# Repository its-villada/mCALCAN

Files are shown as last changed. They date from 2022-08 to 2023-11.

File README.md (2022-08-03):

# mCALCAN
Satélite CANSAT del instituto técnico salesiano Villada. 
Este desarrollo responde a la iniciativa conjunta entre la Comisión Nacional de Actividades Espaciales (CONAE) y el Ministerio de Ciencia, Tecnología e Innovación (MinCyT) tiene como objetivo principal acercar la
ciencia y la tecnología a jóvenes en edad escolar, mediante la participación en la Convocatoria CANSAT Argentina.

## Objetivos
### Misión Primaria
Consiste en el sensado de presión y temperatura y la transmisión de esos datos a la estación terrena,al menos una vez por segundo. Mediante estos dos parámetros calcularemos la altitud, ya que tanto presión como temperatura varían con la altitud.
Para el cálculo de la altura, nuestro CANSAT transmitirá los datos de temperatura y presión antes del despegue y de esa manera obtener los datos iniciales necesarios para el cálculo.
### Misión Secundaria
Aprovechando y como complemento de la misión primaria, la misión secundaria consiste en medir la atmósfera y sus condiciones, con el objetivo de armar un perfil de atmósfera que pueda ser implementado, más adelante, como parte del modelo meteorológico internacional para la generación de pronósticos o la calibración de radares meteorológicos. Esto significa, que se medirán parámetros ambientales de presión y temperatura (tomados en la misión primaria), a los que agregaremos
humedad relativa y porcentaje de CO2. Estos parámetros son medidos y correlacionados con las coordenadas (latitud, longitud y altitud) obtenidas por un módulo GPS.

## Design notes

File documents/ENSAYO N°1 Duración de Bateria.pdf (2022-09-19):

## ENSAYO N°1: Proyecto Mcalcan

Autor: Equipo G.V.I.E

Objeto: Ensayo de duración de batería del CANSAT.

En este ensayo, planteamos experimentar y documentar la duración de las baterías encargadas de alimentar el CANSAT durante el tiempo de misión. Con esto podremos corroborar si la misión se podrá ejecutar con total normalidad con las baterías que contamos.

Condiciones de ensayo iniciales:

- Capacidad de la batería [mAh]: 600 mAh
- Consumo del CAN-SAT en modo operativo (picos): 800 mA
- Consumo del CAN-SAT en modo operativo (corriente promedio): 700 mA
- Voltaje de alimentación de entrada [V]: 7,4 V
- Tiempo de ensayo [m]: 60 m
- Muestras [m]: Cada 5 m

En esta oportunidad vamos a simular al consumo del CANSAT con una carga resistiva cuyo valor en ohmios nos pueda demandar la corriente deseada. Tomaremos muestras con un multímetro conectado a ambas baterías por separado para saber su voltaje.

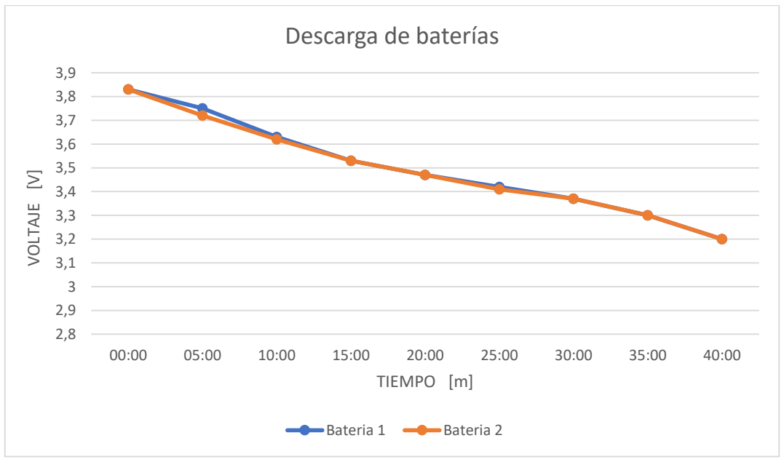
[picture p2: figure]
VOLTAJE [V]; TIEMPO [m]; Descarga de baterías; Bateria 1; Bateria 2

Conclusión: Finalmente llegamos a realizar el ensayo hasta pasados los 40 minutos, ya que las baterías habían llegado a su punto mínimo de descarga. Sin embargo, es una prueba contundente de que nuestra carga útil va a operar con normalidad en los 3-5 minutos que dura dicha misión.

Notas de aplicación:

Realizaremos un cálculo extrapolando la relación de descarga de las baterías en el ensayo previo.

Teóricamente con una batería en óptimas condiciones deberíamos tener, si consumimos 600mA, una duración de 1 hora. Luego del ensayo llegamos a la siguiente relación con respecto a las condiciones reales de la batería.

660mA = 40 minutos

Con esta relación podemos estimar distintos tiempos para distintos consumos. En el caso de que nuestra carga útil este en modo stand-by, consumiendo 100mA. Duraría lo siguiente.
(

660mA
100mA ) ∗ 40 minutos = 264 minutos

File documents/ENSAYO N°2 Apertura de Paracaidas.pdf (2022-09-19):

## ENSAYO N°2: Proyecto Mcalcan

Autor: Equipo G.V.I.E

Objeto: Ensayo de apertura de paracaídas.

En esta oportunidad, planteamos experimentar en la apertura del paracaídas del CANSAT. Para ello nos dirigiremos a las Jarillas, Córdoba (Coordenadas: -31.53743215294978, -64.54285469326625) donde se encuentra un puente con acceso al valle debajo de él. Allí soltaremos un CANSAT señuelo, que este compuesto de la misma estructura y peso que el original, pero sin el hardware dentro. Mediremos la velocidad de descenso y el tiempo de apertura y realizaremos 3 pruebas para poder llegar a un promedio.

Materiales para realizar el ensayo:

- Una balanza.
- Un cronometro.
- Papel y hoja.
- CANSAT señuelo.
- Paracaídas.

Condiciones del primer ensayo:

- Peso del CANSAT señuelo [g]: 306 g
- Medidas del paracaídas:

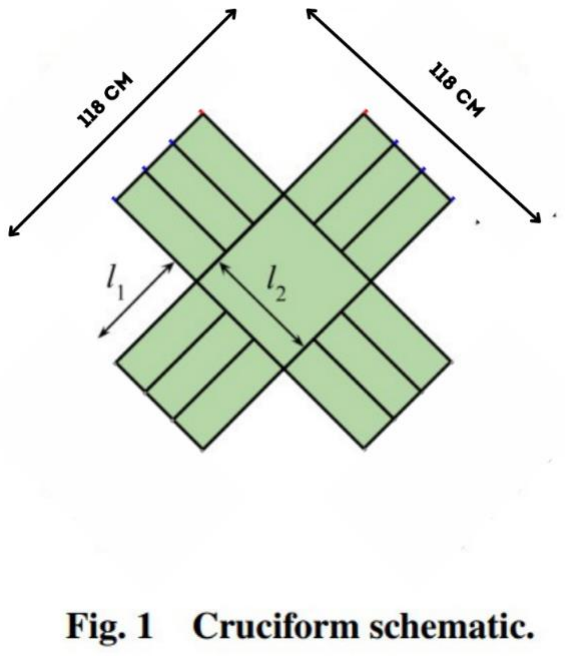
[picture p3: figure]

- Altura de caída libre [m]: 70 m
- Velocidad del viento [m/s]: 4 km/h

- Todos los hilos del mismo largo

Resultado:

El paracaídas al estar enrollado muy fuerte tardó cerca de 4 segundos en abrirse, por lo que tuvo menos desplazamiento en el plano horizontal y además la velocidad del viento era mínima. Sin embargo, en el instante que se abrió el paracaídas la velocidad de caída disminuyo demasiado, aproximadamente a 5,5m/s, lo cual es un punto a favor.

Condiciones del segundo ensayo:

- Peso del CANSAT señuelo [g]: 306 g.
- Medidas del paracaídas:

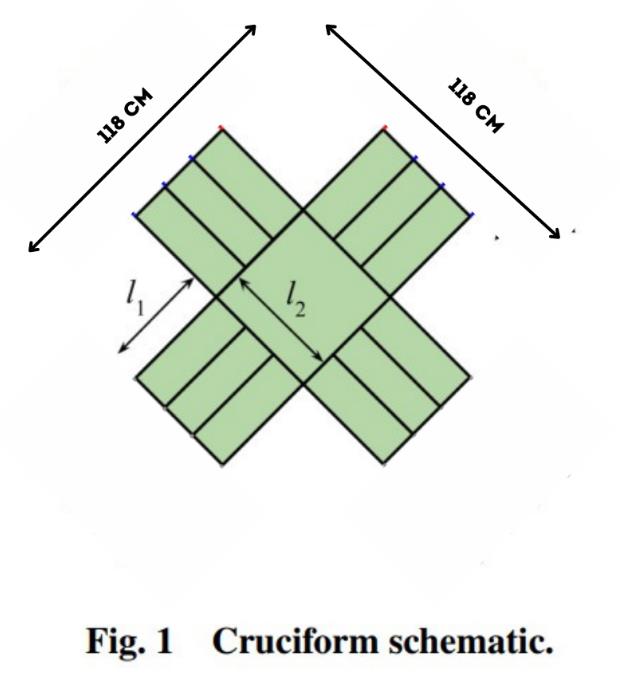
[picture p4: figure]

- Altura de caída libre [m]: 70 m.
- Velocidad del viento [m/s]: 15 km/h.
- Todos los hilos del mismo largo.

Resultado:

Esta vez al estar enrollado de una manera más leve, el paracaídas se abrió casi instantáneamente. A causa del fuerte viento el CANSAT tuvo un desplazamiento horizontal aproximado de 50m con una caída de una velocidad cerca de los 5 m/s.

Conclusión:

El paracaídas para que tenga una repuesta de apertura rápida se debe enrollar de una manera especifica con una tensión de hilos apropiada. Tiene una resistencia muy buena al aire y la tela sylver es la correcta para este tipo de paracaídas.

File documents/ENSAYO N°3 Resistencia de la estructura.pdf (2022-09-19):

## ENSAYO N°3: Proyecto Mcalcan

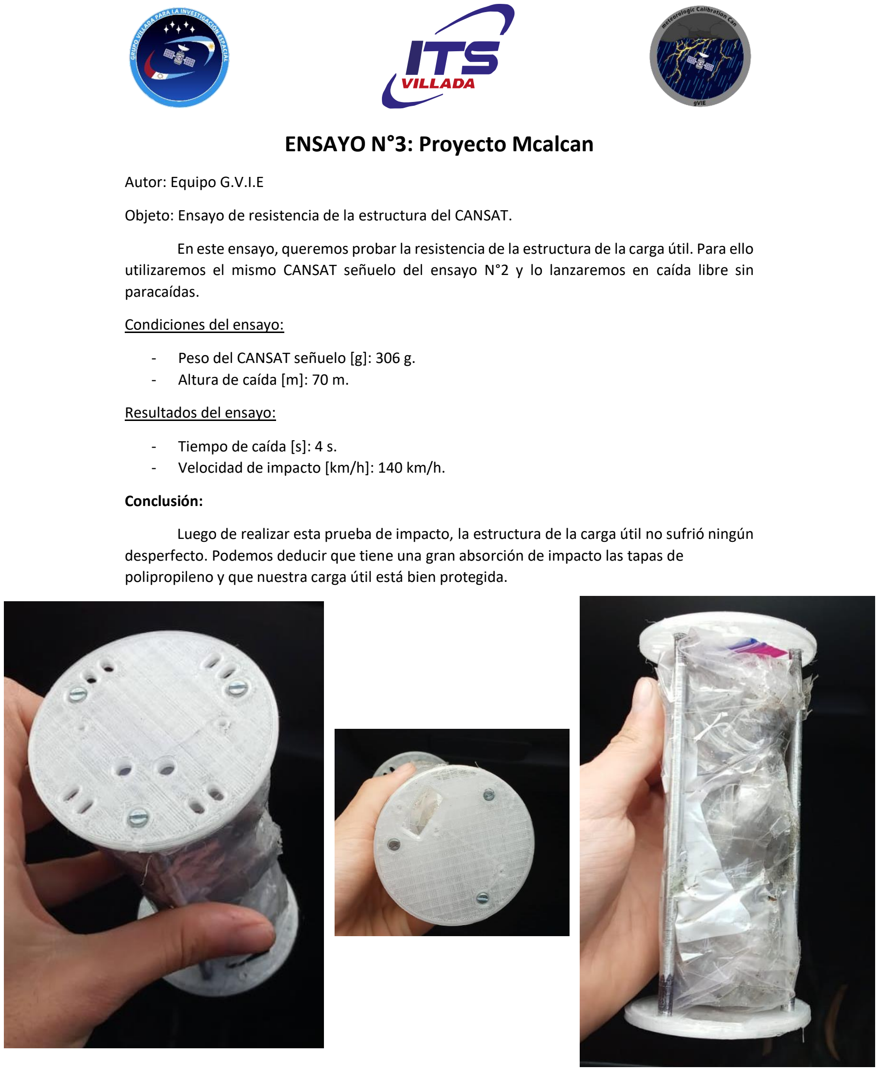
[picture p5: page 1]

Autor: Equipo G.V.I.E

Objeto: Ensayo de resistencia de la estructura del CANSAT.

En este ensayo, queremos probar la resistencia de la estructura de la carga útil. Para ello utilizaremos el mismo CANSAT señuelo del ensayo N°2 y lo lanzaremos en caída libre sin paracaídas.

Condiciones del ensayo:

- Peso del CANSAT señuelo [g]: 306 g.
- Altura de caída [m]: 70 m.

Resultados del ensayo:

- Tiempo de caída [s]: 4 s.
- Velocidad de impacto [km/h]: 140 km/h.

Conclusión:

Luego de realizar esta prueba de impacto, la estructura de la carga útil no sufrió ningún desperfecto. Podemos deducir que tiene una gran absorción de impacto las tapas de polipropileno y que nuestra carga útil está bien protegida.

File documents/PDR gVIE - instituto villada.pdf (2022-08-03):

# mCALCAN

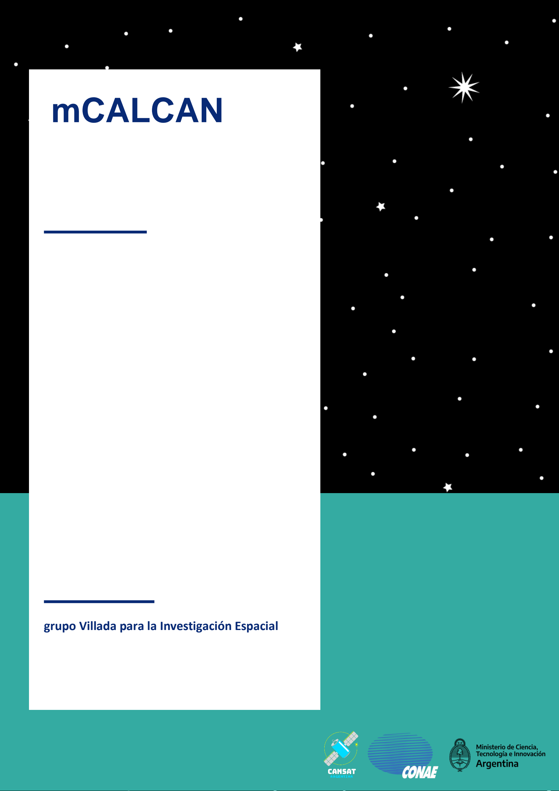
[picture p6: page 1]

1

grupo Villada para la Investigación Espacial

2

Introduccion _______________________________________________________________________ 3

Terminos a Utilizar __________________________________________________________________ 5

Mision ____________________________________________________________________________ 6

Objetivos_______________________________________________________________________________ 6 Misión Primaria ________________________________________________________________________________ 6 Misión Secundaria______________________________________________________________________________ 6

Diseño Preliminar________________________________________________________________________ 8 Layout Físico __________________________________________________________________________________ 8 Como Funciona: Operaciones _____________________________________________________________________ 8

Subsistemas ____________________________________________________________________________ 9 Microprocesador_______________________________________________________________________________ 9 Comunicaciones _______________________________________________________________________________ 9 Sensores _____________________________________________________________________________________ 9 Unidad de Potencia Eléctrica _____________________________________________________________________ 9 Control de Descenso ___________________________________________________________________________ 10 Estructuras __________________________________________________________________________________ 11 Presupuesto de Masas _________________________________________________________________________ 11

Software ______________________________________________________________________________ 12 Programación del Software de Vuelo ______________________________________________________________ 12

Estación Terrena________________________________________________________________________ 13 Configuración ________________________________________________________________________________ 13 Programación de la Estación Terrena ______________________________________________________________ 13

Integración y Pruebas ___________________________________________________________________ 14 Pruebas preliminares de los componentes__________________________________________________________ 14 Secuencia de Integración _______________________________________________________________________ 14 Pruebas de Integridad__________________________________________________________________________ 14 Plan de Validación_____________________________________________________________________________ 15

Operación de la Misión __________________________________________________________________ 16 Secuencia de Eventos prevista ___________________________________________________________________ 16 Roles y Responsabilidades ______________________________________________________________________ 17

Presupuesto ___________________________________________________________________________ 18

Capacidades ___________________________________________________________________________ 19 Capacidades de grupo__________________________________________________________________________ 19 Instalaciones y equipamiento ____________________________________________________________________ 20

Agenda _______________________________________________________________________________ 21

Plan de Documentación__________________________________________________________________ 22

Plan de publicación y Difusión de Resultados_________________________________________________ 23

Enlace al video de presentación ___________________________________________________________ 23

Anexos___________________________________________________________________________ 24

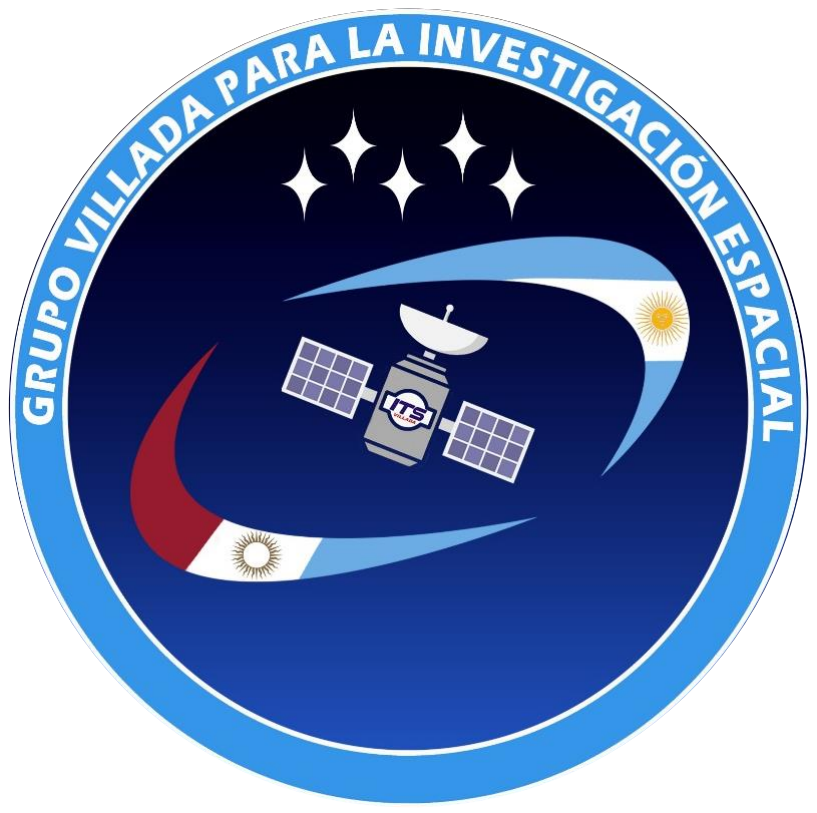
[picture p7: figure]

3

# Introduccion

Nombre del Equipo: grupo Villada para la Investigacion Espacial (gVIE)

Institución: Instituto Tecnico Salesiano Villada

Integrantes del Equipo:
CORTESINI, Luciano
GIL, Ignacio
GIRAUDO, Tomas
LOPEZ, Alejo
PALOMBO, Franco

Docentes:
BEDOURET, Martín
FERRARO, Federico

Parche:

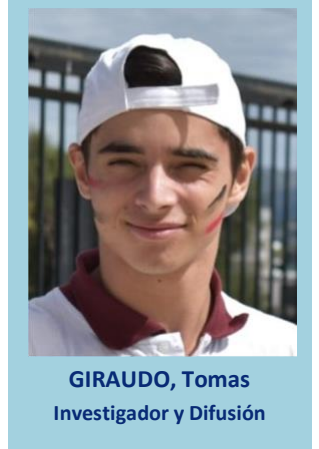
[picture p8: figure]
GIRAUDO, Tomas; Investigador y Difusión

4

Organización del Equipo: Roles

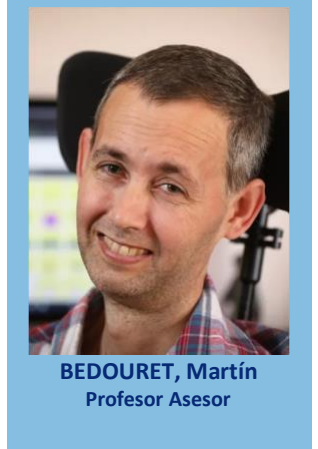
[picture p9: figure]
BEDOURET, Martín Profesor Asesor
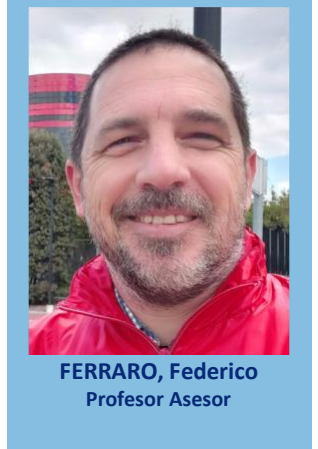
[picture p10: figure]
FERRARO, Federico Profesor Asesor
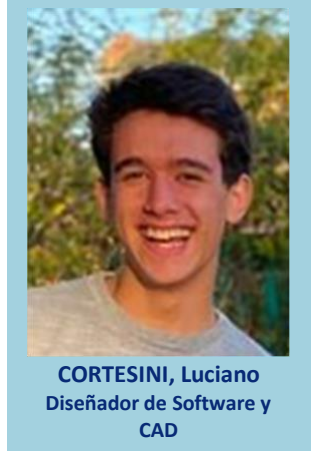
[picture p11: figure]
CORTESINI, Luciano Diseñador de Software y CAD
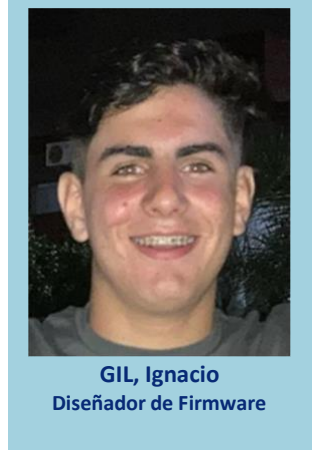
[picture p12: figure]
GIL, Ignacio Diseñador de Firmware
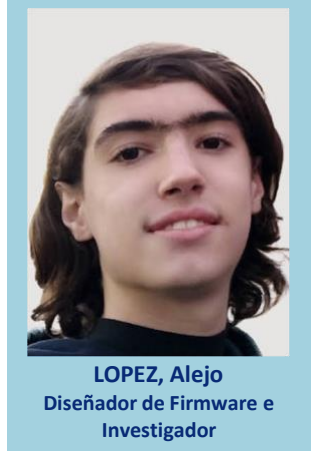
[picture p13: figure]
LOPEZ, Alejo Diseñador de Firmware e Investigador
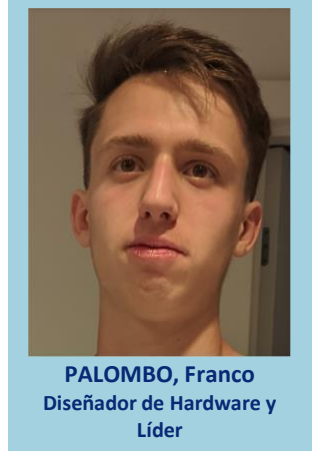
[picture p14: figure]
PALOMBO, Franco Diseñador de Hardware y Líder

5

# Terminos a Utilizar

CPU: Unidad de Procesamiento Central
MCU: Unidad de Microcontrolador
GPS: Sistema de Posicionamiento Global SwPS: Fuente de Alimentación Switching Li-Po: Polímero de litio

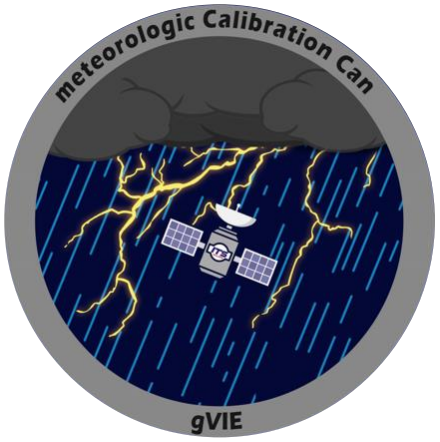
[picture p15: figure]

6

# Mision

Nombre de Mision: mCALCAN (meteorologic Calibration Can)

Parche:

## Objetivos

Misión Primaria
Consiste en el sensado de presión y temperatura y la transmisión de esos datos a la estación terrena, al menos una vez por segundo. Mediante estos dos parámetros calcularemos la altitud, ya que tanto presión como temperatura varían con la altitud.
Para el cálculo de la altura, nuestro CANSAT transmitirá los datos de temperatura y presión antes del despegue y de esa manera obtener los datos iniciales necesarios para el cálculo.

Misión Secundaria
Aprovechando y como complemento de la misión primaria, la misión secundaria consiste en medir la atmósfera y sus condiciones, con el objetivo de armar un perfil de atmósfera que pueda ser implementado, más adelante, como parte del modelo meteorológico internacional para la generación de pronósticos o la calibración de radares meteorológicos. Esto significa, que se medirán parámetros ambientales de presión y temperatura (tomados en la misión primaria), a los que agregaremos humedad relativa y porcentaje de CO2. Estos parámetros son medidos y correlacionados con las coordenadas (latitud, longitud y altitud) obtenidas por un módulo GPS.

El planteamiento de la misión secundaria ronda alrededor de los siguientes puntos:
- Alto costo de las radiosondas meteorológicas:

7

Las radiosondas meteorológicas son dispositivos diseñados para perderse, pero dados los requerimientos de precisión en las mediciones, y las condiciones a las que son sometidas, su costo es bastante elevado (U$D200 en el año 2020). El principio de funcionamiento es que un globo de aproximadamente 6m de diámetro, inflado con hidrógeno, eleva la radiosonda a 30km de la superficie a nivel del mar, para luego explotar y dejar caer la radiosonda de manera incontrolada.
- Inversiones térmicas o scattering de Bragg en las mediciones de las radiosondas
Una inversión térmica, es cuando la temperatura del aire, en vez de descender mientras subimos en altura, como es normal, va ascendiendo cada vez más. Esto genera distorsiones o mediciones erróneas a los radares meteorológicos, los cuales generan perfiles atmosféricos erróneos. La generación de perfiles de atmósfera ayuda a calibrar radares como los que tiene Argentina para poder identificar en ellos estos fenómenos.
- La disminución de los vuelos comerciales por la pandemia:
Esto ha contribuido a tener menos información meteorológica, ya que los aviones en sus ascensos y descensos recolectan estos datos y son utilizados para los modelos de pronóstico.

Este contexto, relevado en el Observatorio Hidrometeorológico de Córdoba, organismo que opera el Radar Meteorológico ubicado en Córdoba Capital, ha servido de input para la definición de nuestra misión secundaria.
Es por eso, que proponemos como solución, la misión mCALCAN. Una opción económica y reutilizable, que permite generar perfiles de atmósfera para poder mejorar las predicciones meteorológicas, y poder aportar al modelo meteorológico internacional más información.

8

## Diseño Preliminar

Layout Físico
Revisar el Anexo: Diseño Preliminar

Como Funciona: Operaciones
El comportamiento esperado del CANSAT es el siguiente:
1. Desde que el CANSAT es cargado en el Cohete, y hasta que inicie el lanzamiento, se mantendrá en reposo para ahorrar energía.
2. Apenas entre en vuelo, el CANSAT comenzará a registrar toda la información y será almacenada en una memoria local.
3. Al momento de la eyección, el CANSAT comenzara la transmisión de datos, mientras paralelamente, sigue almacenando más información. Esto lo hacemos ya que la frecuencia de muestreo guardada en la SD podrá ser mayor a la transmitida, además de para tener redundancia en el caso de una desconexión en la comunicación.
4. Una vez el CANSAT comienza a descender en caída libre, se abrirá el paracaídas, y el sistema de guiado por GPS entrará en juego para comenzar el sistema de fly-back. El CANSAT, tratara de “planear” hasta la ubicación indicada, por medio de actuadores que corrijan el curso de caída hacia el punto designado
5. Luego de que el CANSAT haya aterrizado, emitirá un pitido por medio de un parlante piezoeléctrico y transmitirá la ubicación latitudinal y longitudinal a la estación terrestre para que su localización y recuperación sea más fácil.

9

## Subsistemas

Microprocesador
Se utilizará el microcontrolador Bluepill STM32 provisto por CONAE y MinCyT para realizar la lectura, almacenamiento y transmisión de datos.

Comunicaciones
Se utilizará el módulo LoRA LORA32U4 II provisto por CONAE para la comunicación entre la estación terrena y el CANSAT. Existe la posibilidad que el módulo que está en el CANSAT sea modificado para remover el procesador que incluye el módulo, y solo tener instalado el empaquetado LoRA, sin el microcontrolador que viene incluido. En la estación terrena se utilizará un módulo LoRA idéntico al utilizado en el CANSAT, el cual también será provisto por CONAE. Este módulo LoRA se enlazará al CANSAT y transmitirá todo lo que reciba del mismo a una computadora, a través de un cable USB y el protocolo serial.

Sensores
- Sensor de Presión y Temperatura: BMP180/BMP280, Necesario para la misión
designada por CONAE.
- Sensor de Humedad relativa y Temperatura: AHT10, Se utilizará para medir la
humedad relativa de la atmósfera, necesario para la misión secundaria.
- Sensor de Aceleración e inclinación: MPU6050, este sensor reemplazará al
acelerómetro provisto por CONAE ya que posee giroscopio, lo cual nos permitirá conocer la velocidad angular del CANSAT.
- Sensor de calidad de aire: MQ135, mide múltiples gases tales como: NH3, NOx, Alcohol, Benceno, Humo y CO2. Este sensor nos permitirá conocer la contaminación atmosférica.
- Módulo GPS: uBlox NEO-6M, necesario para obtener las coordenadas del CANSAT y así georreferenciar los datos del perfil atmosférico. También se usará para el control de descenso.

Unidad de Potencia Eléctrica
Para la unidad de potencia eléctrica, se utilizará la batería Li-Po provista por CONAE, en conjunción con una fuente de alimentación switching doble, de tipo buck-boost, con salidas de 5v y 3,3v para poder alimentar todos los sensores y componentes. En caso de que la batería de 1200mAh provista por CONAE sea insuficiente, una batería alternativa sería una celda de Li-ion 18650 de 3.3v, la cual es más grande y pesada pero posee el doble de capacidad, unos 2400mAh.
A continuación, se presenta un cálculo con el tiempo estimado de duración de la batería, dados los cálculos aproximados de potencia, sin tener en cuenta la eficiencia de las fuentes switching:

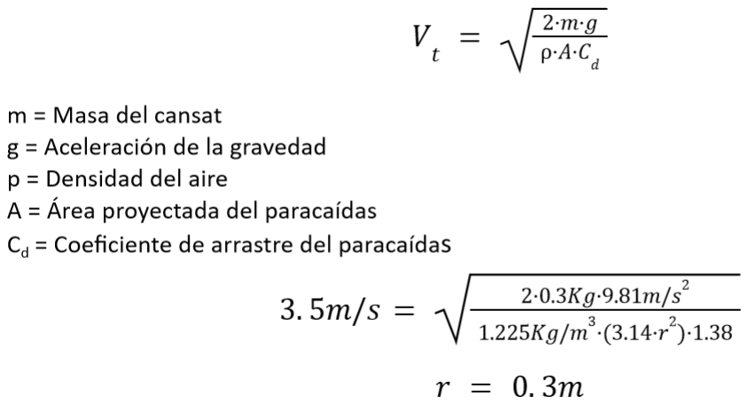
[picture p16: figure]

10

Componente Alimentación(nom) | Corriente(max) | Potencia(max)
STM32 (bluepill) | 3,3 v | 40 mA | 132 mW
LORA32U4 II | 3,3 v | 150 mA | 495 mW
BMP 180/280 | 5 v | 1 mA | 5 mW
MPU6050 | 3,3 v | 5,1 mA | 16,8 mW
uBlox NEO-6M | 3,3 v | 67 mA | 221,1 mW
AHT10 | 3,3 v | 23 uA | 70 uW
MQ135 | 5 v | 160 mA | 800 mW
MicroSD | 3,3 v | 150 mA | 495 mW
Subtotal | 3,3 v – 5 v | 537,12 mA | 2163,3 mW
Potencia Total Máxima Ptot(max) + 10% | 631 mA | 2379 mW

Con la batería que provee CONAE y MinCyT, podríamos tener una duración mínima de 1 hora y 53 minutos, por lo que en teoría, debería ser suficiente para completar la misión.

Control de Descenso
El control de descenso se basa en el objetivo de hacer que el CANSAT vuelva al punto donde despegó o intentar de acercarse lo más cerca posible. A este direccionado lo haremos a partir de un paracaídas que tendrá la posibilidad de ser piloteado a partir de un servomotor. En conjunto con el giroscopio y la ubicación GPS, sabremos hacia qué dirección debemos pilotear en CANSAT. Esto lo hacemos con la idea de poder recuperar el satélite y que no sea una misión de una única vez, sino que se pueda volver a lanzar el CANSAT.

Cálculo de las dimensiones del paracaídas
Para que el tiempo de descenso del CANSAT sea de 85 segundos este debe descender a una velocidad terminal de 3,5 m/s. Para lograr desacelerar la caída libre del cansat hasta la velocidad deseada el paracaídas utilizado será de forma cóncava y tendrá un radio de 0.3 metros. Estos valores se obtuvieron utilizando la fórmula de velocidad terminal, como se detalla a continuación.

11

Estructuras
La estructura de nuestro CANSAT estará formada por dos tapas de aluminio unidas a través de 3 varillas también de aluminio. Entre estas tapas, se colocarán de forma apilada los elementos necesarios, los cuales podemos dividir en 3 principales grupos.
- Sistema de control de descenso
Ubicado en la parte superior del CANSAT, donde se encontrará el servomotor encargado de controlar el paracaídas guiando así al satélite a punto de retorno
- Carga útil
Ubicada en la parte central del CANSAT, es donde se encuentran los sensores que utilizaremos para medir las variables físicas necesarias para cumplir la misión primaria y secundaria.
- Plataforma de servicio
En esta parte de la estructura se ubicarán todos los sistemas necesarios para que el CANSAT funcione: batería, sistema de potencia, sistema de control, comunicaciones.
Los elementos montados sobre las varillas principales de la estructura llevarán unos separadores que cumplirán la función de absorber las aceleraciones aplicadas al CANSAT, para de tal forma, cuidar la integridad de las partes.
Todo esto será recubierto por una carcasa de polipropileno impresa en 3D. Hacemos la elección de este material dadas sus características mecánicas como químicas, además de ser el material de más baja densidad que se comercializa para la impresión 3D por filamento. Para que los datos medidos sean confiables, esta carcasa deberá permitir el flujo de aire a la zona de la carga útil, evitando así fenómenos como el efecto Joule.
Además, la carcasa dispondrá de una apertura que permite remover la batería de CANSAT para su carga.
Presupuesto de Masas
Componente Cantidad | Peso Unitario | Subtotal
STM32 (bluepill) | 1 | 20 g | 20 g
LORA32U4 II | 1 | 20 g | 20 g
BMP 180/280 | 1 | 3 g | 3 g
MPU6050 | 1 | 2 g | 2 g
uBlox NEO-6M | 1 | 12 g | 12 g
AHT10 | 1 | 10 g | 10 g
MQ135 | 1 | 11 g | 11 g
MicroSD | 1 | 2 g | 2 g
PCB | 4 | 6,5 g | 24 g
Batería | 1 | 12 g | 12 g
Servomotor | 1 | 13 g | 13 g
Paracaídas | 1 | 25 g | 25 g
Tapa de Aluminio | 2 | 20 g | 40 g
Varillas de Aluminio | 3 | 10 g | 30 g
Tuercas de Aluminio | 6 | 1,5 g | 9 g
Carcasa Plástica (PP) | 1 | 20 g | 20 g
Separadores de PCB | 3 | 8 g | 24 g
Tornillería | | 20 g | 20 g
| | | TOTAL 297 g

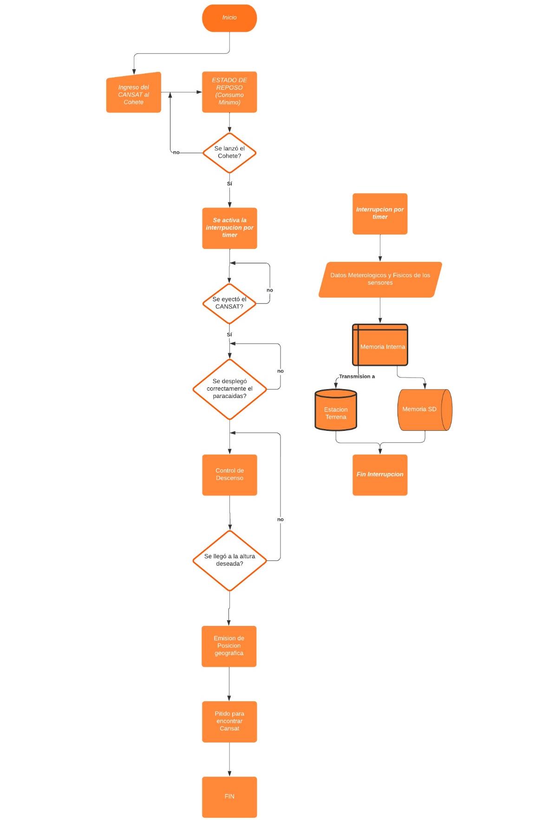
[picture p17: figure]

12

## Software

Programación del Software de Vuelo
Para la programación del software de vuelo, el lenguaje a utilizar, va a ser C y C++, el ide que se utilizará para programar ambos microcontroladores, tanto el bluepill stm32 como el ATmega32u4 de la placa de desarrollo LoRa, es el Arduino IDE, por su facilidad de uso y amplia disponibilidad de librerías y microcontroladores compatibles.

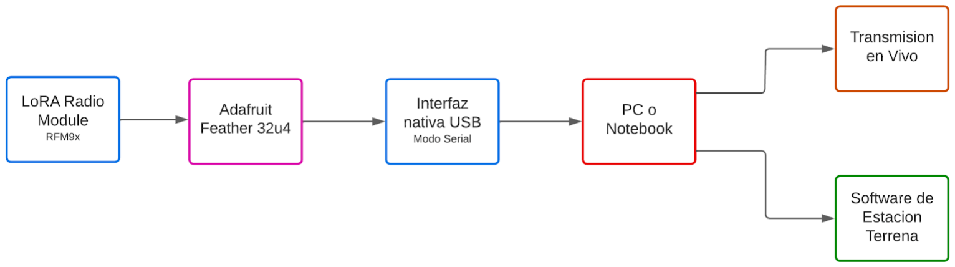
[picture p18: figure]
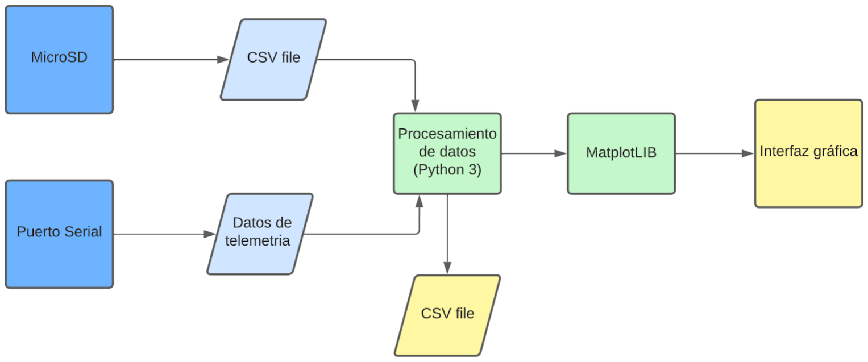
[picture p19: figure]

13

## Estación Terrena

Configuración
Diagrama en bloques del hardware:

Diagrama en bloques del software:

Programación de la Estación Terrena
La estación terrena estará equipada con un front-end con una interfaz de usuario que exponga múltiples gráficos sobre variables del CANSAT mismo, y los parámetros a medir, como también estados lógicos. Toda esta información será mostrada de dos formas:
a. Por medio de una computadora
b. Por medio de una transmisión por vía YouTube, con el agregado de una grabación en vivo del lanzamiento

El software de la estación terrena, desarrollado en Python 3, será capaz de leer desde el puerto serial de la computadora todos los datos recibidos por el módulo LoRa, mostrando a través de una interfaz gráfica todos los datos recopilados por el CANSAT y guardando estos datos en un archivo .CSV, además de mostrar valores de interés tales como nivel de batería, posición, etc.
Además, el software será capaz de leer el archivo .CSV guardado en la microSD del CANSAT y convertirlos en un gráfico para su fácil interpretación.

14

## Integración y Pruebas

Pruebas preliminares de los componentes
Todos los sensores serán testados individualmente previo al ensamblado del CANSAT y las mediciones serán contrastadas contra sensores calibrados, para asegurar el correcto funcionamiento de los sensores.
Para probar el funcionamiento de los módulos LoRA se establecerá un enlace simple entre dos computadoras cada una con su respectivo módulo y se comprobará el correcto envío y recepción de datos entre las mismas, así como el alcance y velocidad de enlace de los módulos LoRA.

Secuencia de Integración
1. Se parte de una base de aluminio la cual posee 3 varillas que cumplirán la función de columnas.
2. Se colocarán una por una las distintas PCBs las cuales poseen entre ellas un separador de goma.
3. Las PCBs se conectarán entre sí en el mismo momento de colocación ya que poseerán pines macho-hembra que entrarán en contacto al colocar la placa.
4. En la parte superior se colocará el sistema de control de descenso.
5. Se colocará la tapa superior del cilindro la cual se asegurará a las columnas a través de una tuerca y contratuerca,
6. Se colocará el cilindro exterior de la estructura(carcasa), el cual irá fijado a través de tornillos.
7. Se coloca, fija y conecta la batería a través de la apertura de la carcasa destinado a esto
8. Se fijará el paracaídas a la tapa superior con la ayuda de las ranuras destinadas a esto.
9. Se realizarán las pruebas de integridad y comunicaciones.
10. El CANSAT se encuentra listo para colocarse en el cohete.

Pruebas de Integridad
Una vez ensamblado el CANSAT se realizarán ensayos no destructivos para asegurarnos de que todos los subsistemas cumplan su función adecuadamente.
Se lanzará el CANSAT desde distintas alturas y con variadas velocidades angulares para comprobar el descenso controlado. Durante estas pruebas nos aseguraremos de no dañar la estructura del CANSAT. Para asegurarnos que el CANSAT siga funcionando, es decir siga midiendo correctamente los parámetros ambientales y enviando los datos a la estación terrena, pese a las altas aceleraciones y vibraciones, buscaremos alguna manera de probar el CANSAT en condiciones lo más similares posibles a las condiciones que existirán durante la misión.
Se encenderá el CANSAT y se dejará en estado de reposo (estado previo al lanzamiento) y en estado activo (Recopilando datos y enviándolos) durante tiempos varias veces mayor al que existirá durante la misión, esto para asegurarnos que no existan fallas en el código, como overflows de memoria o loops infinitos imprevistos, también para comprobar el comportamiento de la batería.

15

Plan de Validación
Para validar que nuestro CANSAT cumpla con los requerimientos de tamaño y peso determinados por el CONAE, imprimimos en 3D un cilindro cuyas dimensiones internas sean las máximas permitidas y nos aseguraremos de que nuestro CANSAT entre dentro de este cilindro. Para validar el peso del CANSAT utilizaremos una balanza de precisión.
Se prevee la fabricación de un “CANSAT dummy” con los mismos materiales, pesos y tamaños que el CANSAT final. Este dummy será lanzado desde una altura determinada, usando el sistema de descenso controlado diseñado por nosotros, los datos recopilados durante esta prueba luego se extrapolan para obtener una aproximación al comportamiento del CANSAT durante la misión. Este dummy también se utilizará para realizar ensayos destructivos y comprobar la integridad y resistencia física de nuestro CANSAT.

16

## Operación de la Misión

Secuencia de Eventos prevista
La misión se va a separar de 7 etapas:
- Etapa 1: Preparación de la estación terrena
Esta etapa es la que se ejecuta al llegar al lugar de lanzamiento. Consta de preparar la transmisión en vivo por la plataforma YouTube, la puesta en marcha de los programas de monitoreo y recepción y la conexión con el CANSAT y la Estación Terrena.
- Etapa 2: Prueba de comunicación y Prueba de sensores
Esta etapa es más que nada una verificación redundante, pero nos asegura la puesta en punto de los sensores y su correcto funcionamiento. En esta instancia, nos conectaremos al CANSAT desde la Estación terrena, y trataremos de simular algunas de las situaciones que se puedan presentar durante el lanzamiento (cambios de temperatura, %HR, y otros) para poder confirmar el correcto funcionamiento de todos los sensores.
- Etapa 3: Preparación para el lanzamiento
En esta etapa, se realizará la instalación del CANSAT en el cohete, y se colocará en modo de suspensión para ahorrar batería hasta que la interrupción indicada lo despierte.
- Etapa 4: Lanzamiento y Alcance del Apogeo
Durante esta etapa, se realizará un monitoreo básico y de baja frecuencia de las condiciones internas del CANSAT, tales como tensiones, temperaturas, posición y aceleraciones.
- Etapa 5: Recolección de datos en tiempo real y recuperación del CANSAT
Esta etapa consta de la recepción de la información en tiempo real que recupera el CANSAT, desde que llega al apogeo, hasta entrar en contacto con la superficie. Una vez llegado a la superficie, un equipo va a buscar el CANSAT en las coordenadas que transmitió antes de caer para recuperar la tarjeta de memoria.
- Etapa 6: Procesado de la información en tiempo real y local del CANSAT
Esta etapa consiste en comparar la información recibida y la información que se almacenó de manera local en el CANSAT para poder hacer gráficos, y poder confirmar que la información que se envió es la misma que está almacenada de manera local.
- Etapa 7: Compilación de información recogida
En esta etapa, se conformarán gráficos y resultados de fórmulas que serán los cuales serán utilizados más adelante para calibrar radares y modelos meteorológicos.

17

Roles y Responsabilidades
Franco Palombo: Supervisor de la misión
Tomas Giraudo: Encargado de difusión y transmisión en vivo
Luciano Cortesini: Operario de la Estación Terrena
Alejo López: Preparación y lanzamiento del CANSAT / recuperación del CANSAT Ignacio Gil: Preparación y lanzamiento del CANSAT / recuperación del CANSAT

18

## Presupuesto

Denominación Nro. de Mod. | Precio Unit. | Cantidad Subtotal
Sensor de Humedad y
Temperatura
| AHT10 | 600 AR$ | 1 | 600 AR$
Acelerómetro + Giroscopio | MPU 6050 | 700 AR$ | 1 | 700 AR$
Sensor de calidad de Aire | MQ135 | 550 AR$ | 1 | 550 AR$
Modulo GPS | uBlox NEO-6M | 2000 AR$ | 1 | 2000 AR$
PCB Virgen | 10x10cm | 300 AR$ | 2 | 600 AR$
Impresiones 3D | - | 300 AR$ | 1 | 300 AR$
Componentes Discretos/pasivos | - | 500 AR$ | 1 | 500 AR$
Varillas de Aluminio | D5mm L13mm | 250 AR$ | 3 | 750 AR$
Tornillería | - | 500 AR$ | 1 | 500 AR$
Círculos de Aluminio | D7mm E2mm | 50 AR$ | 2 | 100 AR$
TOTAL 6600 AR$

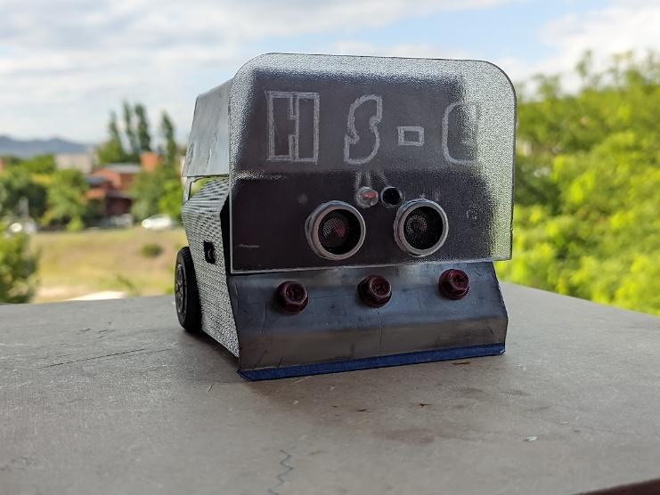
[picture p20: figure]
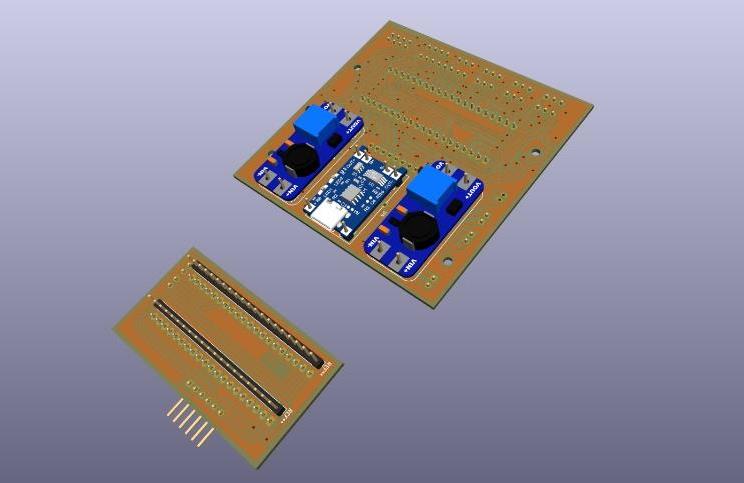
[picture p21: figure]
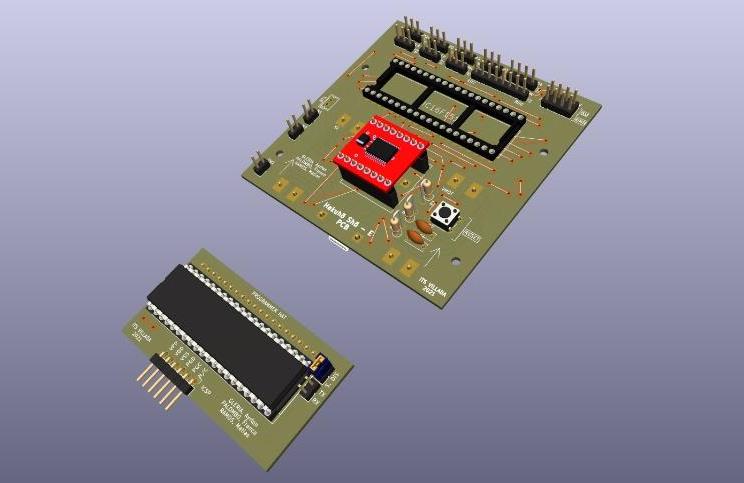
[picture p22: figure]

19

## Capacidades

Capacidades de grupo
Somos alumnos de 7mo año de un colegio técnico, con especialidad en electrónica. Por lo que nuestro grupo posee plena capacidad para llevar a cabo la misión CANSAT. Tenemos experiencia en el diseño y armado de circuitos impresos (PCBs), programación de microcontroladores con el lenguaje C, electrónica discreta, diseño e impresión 3D.

Nuestra participación en las Olimpiadas Nacionales de Innovación, Informática, Electrónica y Tecnología aplicada (ONIET 2020)
- Luciano Cortesini: 2do puesto en electrónica discreta
- Franco Palombo: 2do puesto en programación de microcontroladores.
- Ignacio Gil: 3er puesto en programación de microcontroladores.

Algunos ejemplos de nuestras capacidades en proyectos anteriores
Este proyecto es un Mini-sumo llamado “Hakuhō Shō – E”. Fue llevado a cabo durante el ciclo lectivo 2021. El objetivo de este proyecto era competir con otros grupos (de 3 integrantes) de alumnos del mismo colegio para determinar quién destacaba más en 3 áreas: Diseño de firmware automatizado, Diseño de Hardware y estrategia de trabajo.

20

Instalaciones y equipamiento
Contamos con un laboratorio de electrónica completamente equipado. Tenemos lo necesario para el armado de PCBs desde cero (Ácido, planchas, placas vírgenes, soldadoras, perforadora dremel), contamos con instrumentos de medición eléctrica como multímetros y osciloscopios, herramientas para la construcción de la estructura del CANSAT, impresoras 3D y demás herramientas para llevar a cabo la misión. También contamos con talleres mecánicos, con tornos, fresadoras, plegadoras de chapa, perforadoras, herramientas de corte y los materiales necesarios para fabricar la estructura del CANSAT.

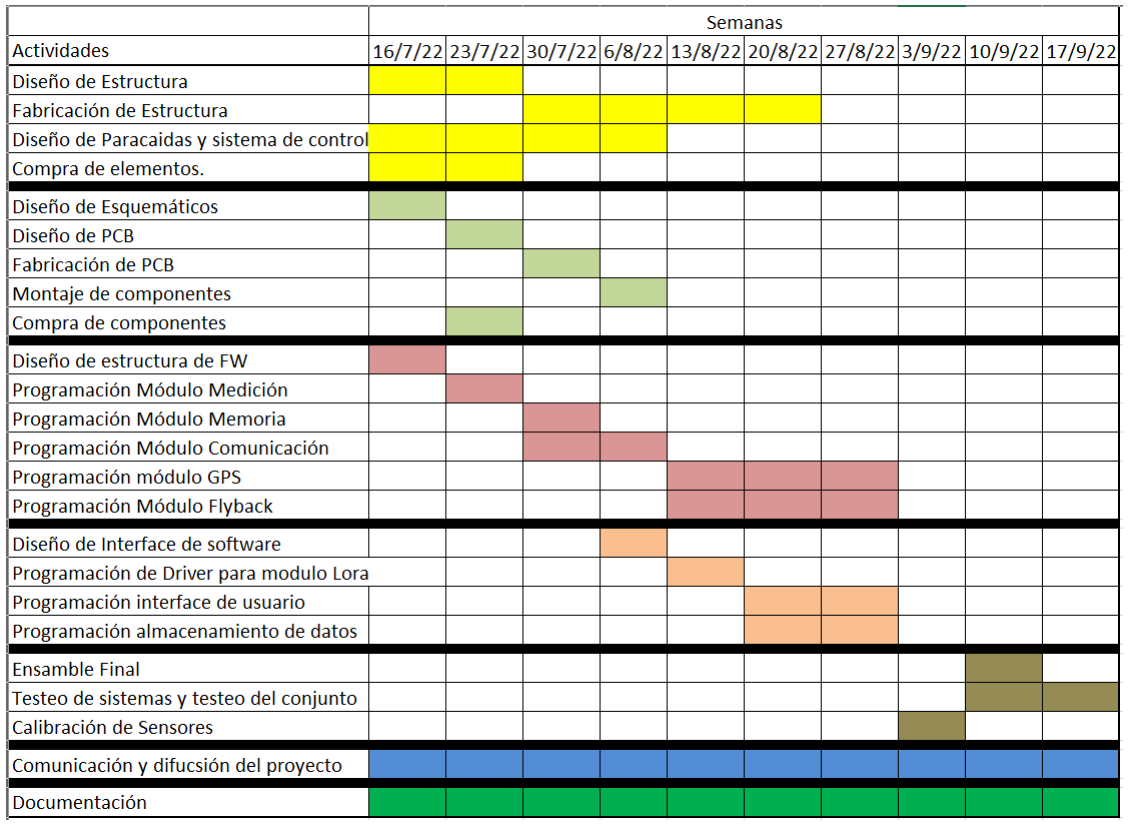
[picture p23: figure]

21

## Agenda

22

## Plan de Documentación

El plan de documentación que hemos planeado para este proyecto consiste en archivar todos los aspectos del mismo, por medio de la plataforma de GitHub y un drive de Google con acceso gratuito como lector. En ellos incluimos fotos, videos, códigos de programación, progreso del proyecto, diseños, etc.
Todos los enlaces con acceso a estas distintas plataformas, serán compartidos por nuestras redes sociales planteadas en nuestro plan de difusión.

23

## Plan de publicación y Difusión de Resultados

Nuestro plan de Difusión y Publicación de nuestro proyecto CANSAT de tanto, nuestro trayecto inicial como los procesos de fabricación y lanzamiento, se dirige a dos tipos de públicos.
- El primer objetivo de publicidad va destinado a investigadores, científicos, meteorólogos, integrantes de la CONAE, que quieran conocer los datos que pudimos recolectar en nuestra misión mCALCAN. La manera de poder difundir estos datos para que sean accesibles dentro de la comunidad científica es por medios de documentos científicos publicados en plataformas de lectura libre, como lo es la biblioteca virtual del CONICET. De esta forma, podemos generar un gran impacto dentro de la comunidad científica y podremos dar a conocer nuestro proyecto CANSAT
- El segundo objetivo, es poder llevar CANSAT a todas las escuelas del país para que la conozcan, por medio de redes sociales (como Instagram, You-Tube, Tik-Tok, Twitter). En ellos documentamos todo el proceso, desde el planteamiento de idea, el proceso de diseño, el proceso de fabricación y materialización, todas las pruebas físicas y de vuelo que le haremos a nuestro CANSAT, hasta el lanzamiento final mediante streaming o LIVE.

Este público al cuál queremos dar a conocer nuestra misión y nuestro trabajo, lo hacemos con la finalidad de que se despierte el interés de participar en estos programas propuesto por la CONAE, a las futuras generaciones de las distintas escuelas secundarias del país, y que puedan ser parte del proyecto CANSAT en sus próximas ediciones.

Nuestras redes sociales son:
- Instagram: @g.v.i.e
- YouTube: Grupo G.V.I.E
- Tik-Tok: @G.V.I.E_22

VIDEO DE PRESENTACIÓN
https://www.youtube.com/watch?v=hTsHWQAWCgM Video Presentación Grupo G.V.I.E - Cansat Argentina 2022 (https://youtu.be/hTsHWQAWCgM)

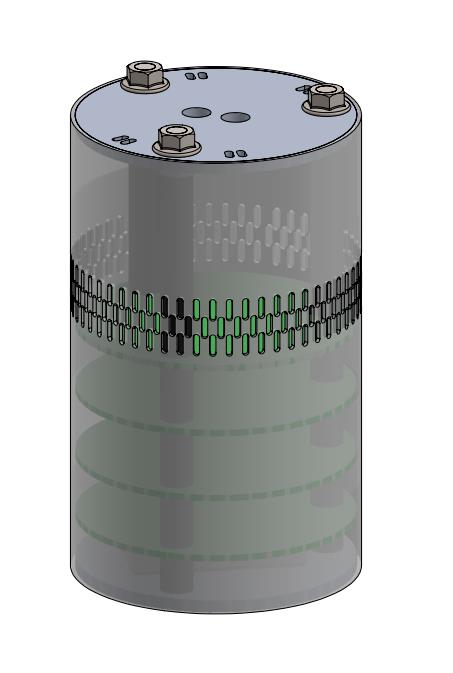
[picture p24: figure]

24

# Anexos

Anexo A - diseño preliminar

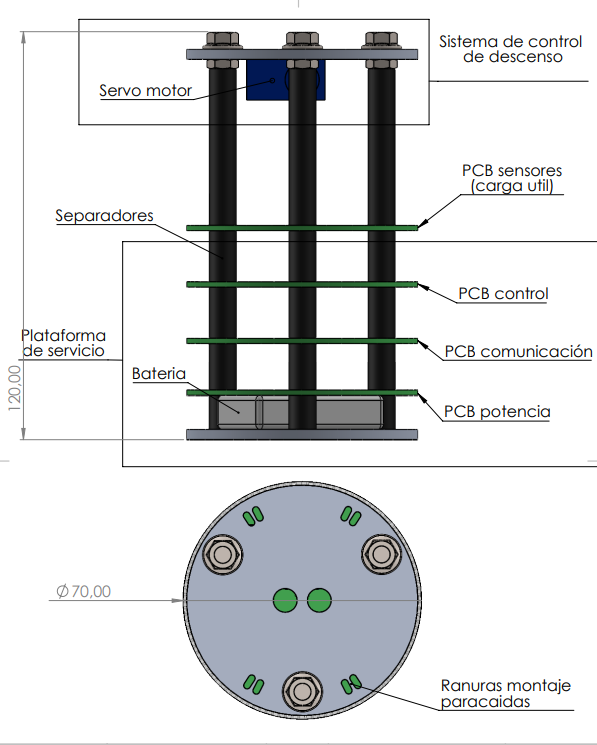
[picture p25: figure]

25

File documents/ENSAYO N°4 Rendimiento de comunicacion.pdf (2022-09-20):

## ENSAYO N°4: Proyecto Mcalcan

Autor: Equipo G.V.I.E

Objeto: Ensayo de estabilidad de comunicación entre la estación terrena y la carga útil.

En este ensayo, vamos a dar a prueba la estabilidad de comunicación entre ambos dispositivos. Para ello realizaremos un procedimiento de transmisión constante de datos durante una cierta cantidad de tiempo con una tasa de refresco determinada y veremos los resultados.

Condiciones del ensayo:

- Protocolo de comunicación: Radio LoRa.
- Distancia entre dispositivos [m]: 3 m.
- Tasa de refresco [ms]: 500 ms.
- Duración de transmisión [hs]: 2 hs.
- Revisión de funcionamiento [m]: Cada 15m.

Resultados:

Muestra | Tiempo [m] | Descripción
1 | 15:00 | FUNCIONANDO OK
2 | 30:00 | FUNCIONANDO OK
3 | 45:00 | FUNCIONANDO OK
4 | 60:00 | FUNCIONANDO OK
5 | 75:00 | FUNCIONANDO OK
6 | 90:00 | FUNCIONANDO OK
7 | 105:00 | FUNCIONANDO OK
8 | 120:00 | FUNCIONANDO OK

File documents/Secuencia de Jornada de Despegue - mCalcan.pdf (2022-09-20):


# SECUENCIA DE DESPEGUE

## mCalcan

### tomas giraudo

### ITS Villada

G.V.I.E. Alumnos de 7mo “B”

## Contents

## Introducción

En el siguiente documento se presenta los puntos a ser considerados en el momento del despegue de nuestro CANSAT. Estos deberán ser seguidos paso a paso para el correcto lanzamiento de la carga útil.

## Viaje a CONAE

Se presenta a continuación todos los elementos necesarios para el correcto desarrollo de la jornada de despegue en la CONAE, donde cada uno de los integrantes deberá ocuparse de cada ítem:

TOMAS | ALEJO | IGNACIO | LUCIANO | FRANCO
Herramientas (Alicates, pinzas, soldador, destornilladores) | Lector de tarjetas SD | Estación Terrena MK2 | Estructura de repuesto | CANSAT con todas sus partes
Estaño | 2 computadoras, cargadas al 100%, con la última versión de estación terrena (software de Python) | Televisor | Mesa y sillas plegables | Paracaídas
Cinta aislante | | Cable HDMI

Hilo dental

Inversor

## Preparación

Antes del pre-despegue se deberán tener los siguientes elementos preparados:

TOMAS | ALEJO | IGNACIO | LUCIANO | FRANCO
Cámara de video con batería y espacio de almacenamiento libre y empezar a documentar. | Ambas baterías Li-Po cargadas (Medirlas previamente). | Ultima versión de códigos testeados, subidos a los microcontroladores. | CANSAT armado, verificando los pasos explicados debajo. | Estación terrena conectada y funcionando.

## Armado del CANSAT:

Luciano Cortesini se encargará del Armado de nuestra carga útil.

- Primero presentamos la tapa inferior de la estructura y atornillamos las 3 varillas laterales.
- Colocamos las baterías con su respectivo soporte y lo atornillamos.
- Colocamos 3 separadores y seguido colocamos la placa de alimentación.
- Colocamos 3 separadores y seguido la placa de control.
- Colocamos 3 separadores y seguido la placa de telemetría.
- Colocamos 3 separadores y seguido la primera placa de sensores.
- Colocamos 3 separadores y seguido la segunda placa de sensores.
- Atornillamos los servos en la tapa superior.
- Acondicionamos los hilos del paracaídas en la tapa y en la polea de los servos.
- Conectamos todas las placas entre sí y verificamos que encienda el CANSAT.
- Recubrimos la carga útil con la carcasa externa.
- Cerramos la carga útil con la tapa superior y atornillamos.
- Enrollamos el paracaídas.

## FRANCIO PALOMBO SUPERVISARÁ TODA LA MISIÓN:

## Pre-Despegue:

LUCIANO CORTESINI:

- Verificar seguridad de la estructura y del paracaídas.

IGNACIO GIL:

- Enviar primer comando (gvie,0,12), donde se inicializarán la latitud y longitud donde queremos que nuestro satélite aterrice.
- Enviar el comando de listo para despegar (gvie,0,03) que encenderá todos los sensores, medirá la presión base y enviará telemetría durante 15 segundos. Verificaremos que todos los sensores estén funcionando correctamente.

## Fase de Despegue:

ALEJO LOPEZ:

- Acoplar la carga útil en el cohete teniendo en cuenta su previo armado y probado el protocolo de launch-phase.

TOMAS GIRAUDO:

- Comenzar grabación de lanzamiento.

FRANCO PALOMBO:

- Grabar pantalla de la Interfaz Gráfica.
- Enviar comando de iniciar misión.
- Dar Ok para el lanzamiento.

## Fase de despliegue:

IGNACIO GIL:

- Verificar que la Estación terrena está recibiendo los datos.
- Esperar a que el CANSAT realice la misión.
- Finalizar Grabado de pantalla de la Interfaz Gráfica luego de aterrizaje.

## Recuperación del CANSAT:

IGNACIO GIL:

- Enviar petición de coordenadas de ubicación del CANSAT.
- Enviar comando para reproducir la melodía del buzzer.

LUCIANO CORTESINI Y ALEJO LOPEZ:

- Recuperar carga útil.

TOMÁS GIRAUDO:

- Documentar todo el proceso.

## Transferencia de datos:

IGNACIO GIL:

- Conectar la carga útil a la base de la Estación terrena.
- Descargar los datos recolectados en la micro SD.

## Post-Procesado de video:

TOMÁS GIRAUDO:

- Realizar edición de video final para publicar en redes sociales.

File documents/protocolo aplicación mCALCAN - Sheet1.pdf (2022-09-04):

header | tipo | request/response code | datos (opcional)
g | v | i | e | 0 | 2 | 1

Tipo (1 byte)

Esto describe el tipo de mensaje en dos tipos: solicitud o respuesta. Solicitud

0 : Confirmable : This message expects a corresponding acknowledgement message.

1 : Non-confirmable : This message does not expect a confirmation message.
Respuesta

2 : Acknowledgement : This message is a response that acknowledge a confirmable message

3 : Reset : This message indicates that it had received a message but could not process it. 4: Error: Se utiliza para informar algun error

Código de solicitud/respuesta (2 bytes)

El primer byte indica la operación a ejecutar 0: leer datos y solicitud de información

1: escribir datos
2: ejecutar acción

3:borrar, reset

El segundo byte indica el elemento o acción específica

0: iniciar misión.
1: se aborta la misión de flyback, aterrizar donde se encuentre el cansat.

2: ubicación del aterrizaje

3: listo para despegar

4: Telemetria completa

5: Resetear memoria eeprom del cansat

7: Indeterminado.

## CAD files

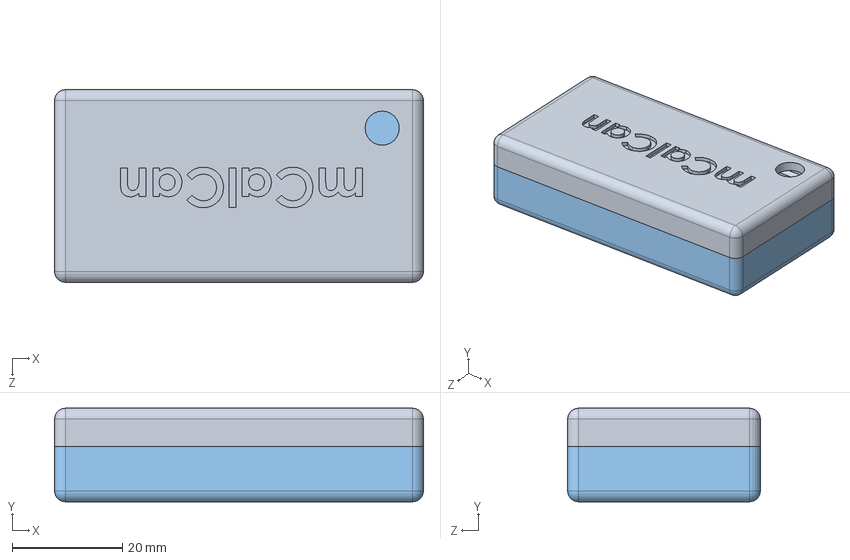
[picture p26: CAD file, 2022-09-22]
3D models/estacion terrena/carcasa ET.SLDASM
67.0 x 17.0 x 35.0 mm
Carcasa ET arriba
pcb ET
Carcasa ET

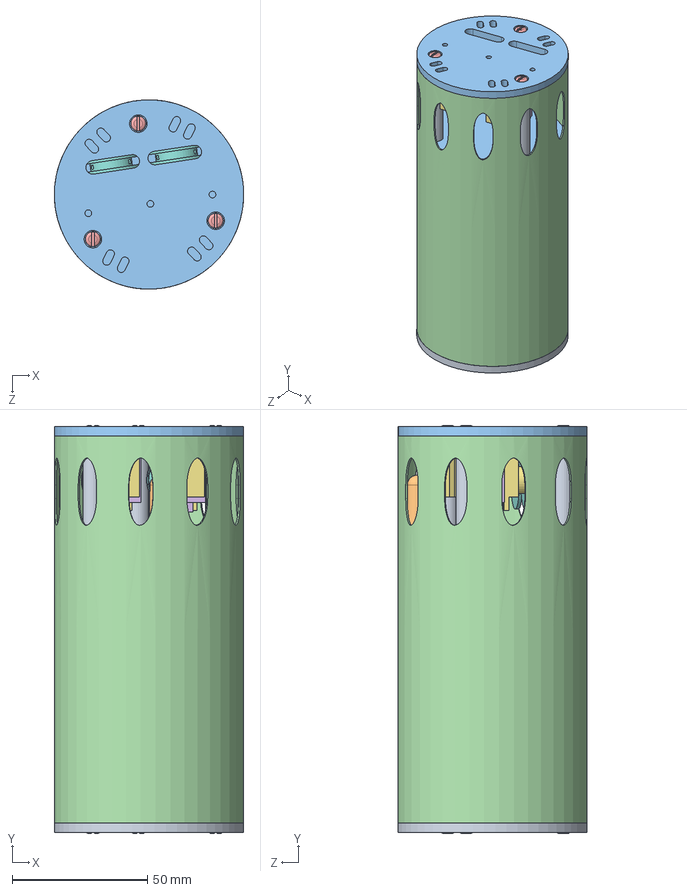
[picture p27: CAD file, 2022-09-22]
3D models/mCalCan/MCalCanV2.SLDASM
70.0 x 150.8 x 70.0 mm
TAPA INFERIOR
VARILLA x 3
TAPA SUPERIOR
Carcasa
pan slot head_am x 6
hex nut jam_am
pan cross head_am x 2
bateria x 2
Separador x 18
Antena
PCB x 5
IDC Female
soporte bateria V2
soporte servosv2
servo x 2
polea x 2

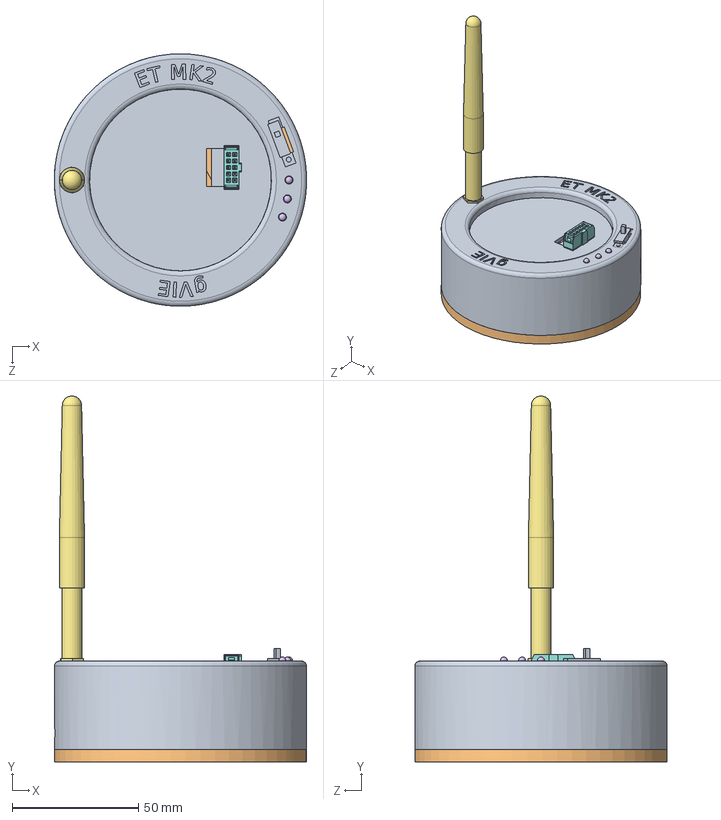
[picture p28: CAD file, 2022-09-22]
3D models/Estacion Terrena v2/MARK1-V1.SLDASM
100.0 x 145.0 x 100.0 mm
Carcasa superior
LED-3mm.stp x 3
Antena
10 pin female idc
sw
TapaInferior

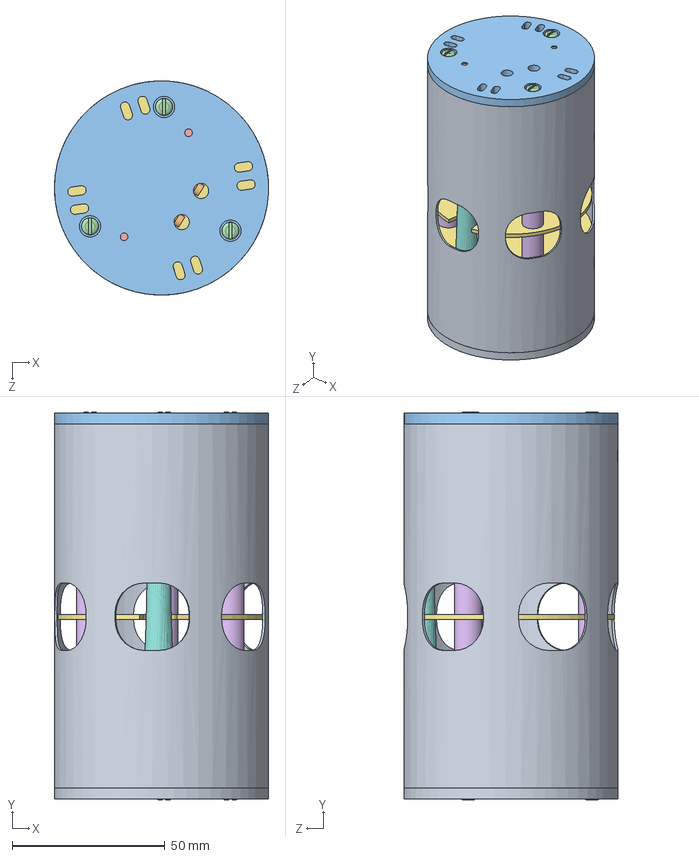
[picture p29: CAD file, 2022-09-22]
3D models/mCalCan/MCalCanv1.SLDASM
70.0 x 126.8 x 70.0 mm
TAPA INFERIOR
VARILLA x 3
TAPA SUPERIOR
pan slot head_am x 8
pan cross head_am x 5
hex nut style 1_am x 2
e-ring external retaining ring_am x 3
hex nut jam_am
servo x 2
soporte servos
bateria
soporte bateria
Separador x 18
PCB x 5
Antena

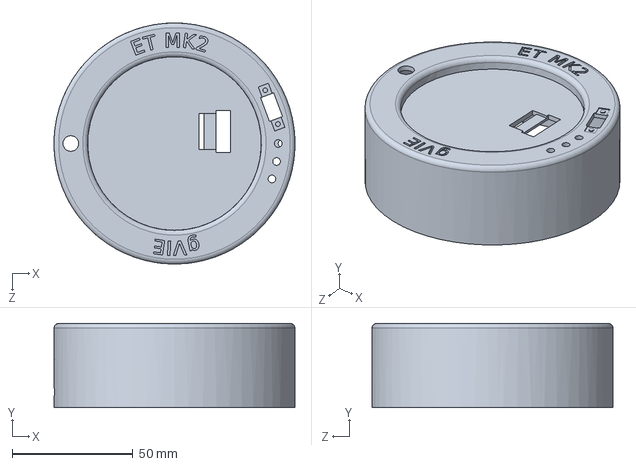
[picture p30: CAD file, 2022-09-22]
3D models/Estacion Terrena v2/Carcasa superior.SLDPRT
100.0 x 35.0 x 100.0 mm

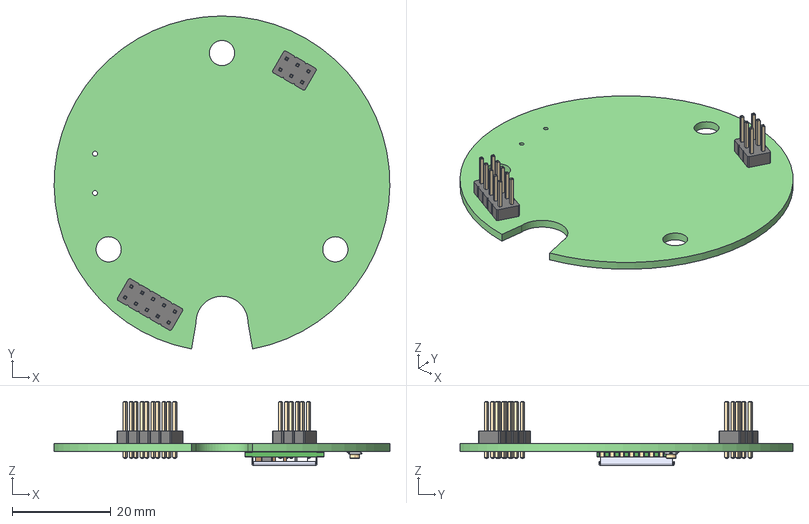
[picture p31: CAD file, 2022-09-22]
3D models/mCalCan/PCB/PCB3.step
68.0 x 67.4 x 13.0 mm
_autosave-PCB5 PCB

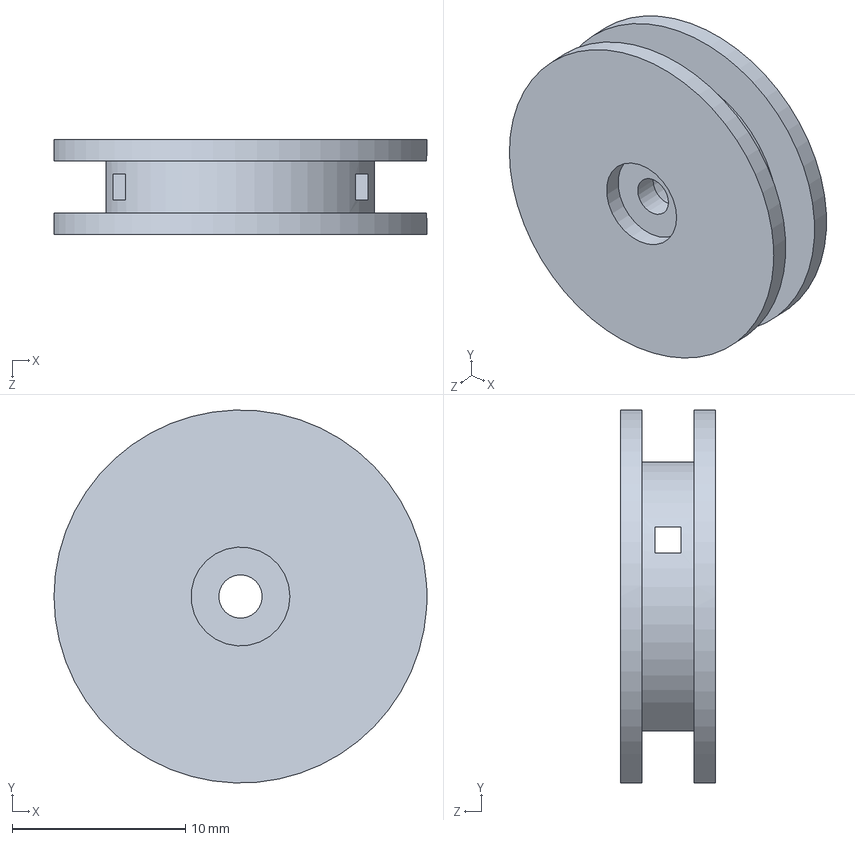
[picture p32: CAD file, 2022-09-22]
3D models/mCalCan/polea.SLDPRT
21.5 x 21.5 x 5.50 mm

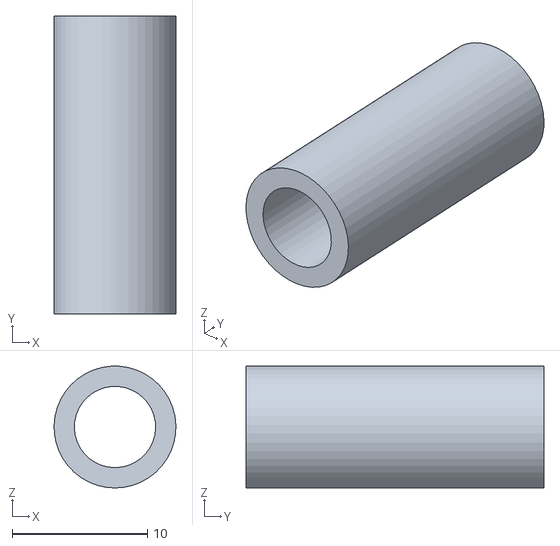
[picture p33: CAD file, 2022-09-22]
3D models/STL/Separador22.STL
8.99 x 22.0 x 9.00

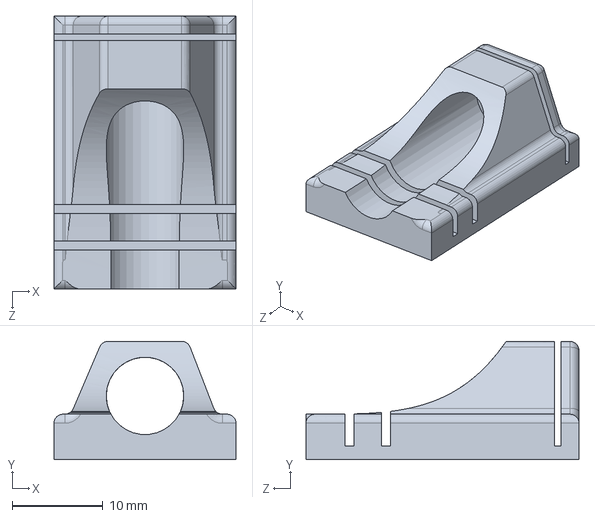
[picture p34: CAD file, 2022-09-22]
3D models/varios/Corta separadores.SLDPRT
20.0 x 13.0 x 30.0 mm

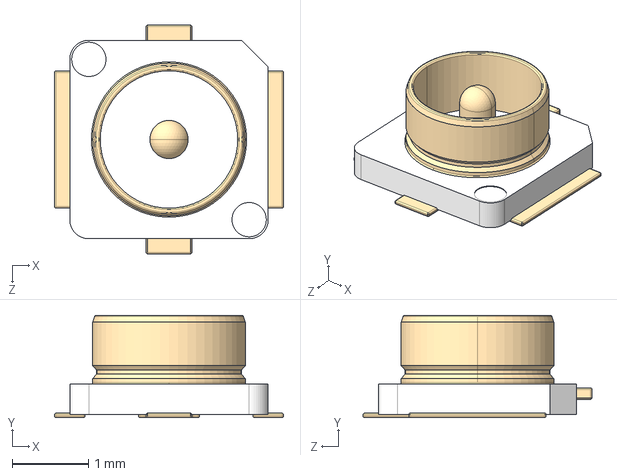
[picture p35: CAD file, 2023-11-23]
sch/mCALCAN_lib.3d/RSP-122811-01--3DModel-STEP-56544.STEP
3.00 x 1.34 x 3.00 mm

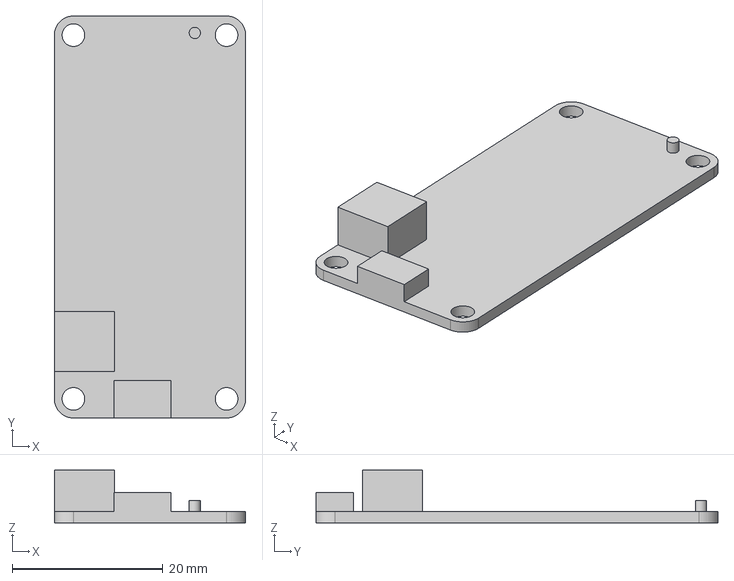
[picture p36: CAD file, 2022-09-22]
3D models/Estacion Terrena v2/LoRa.step
25.4 x 53.3 x 7.00 mm

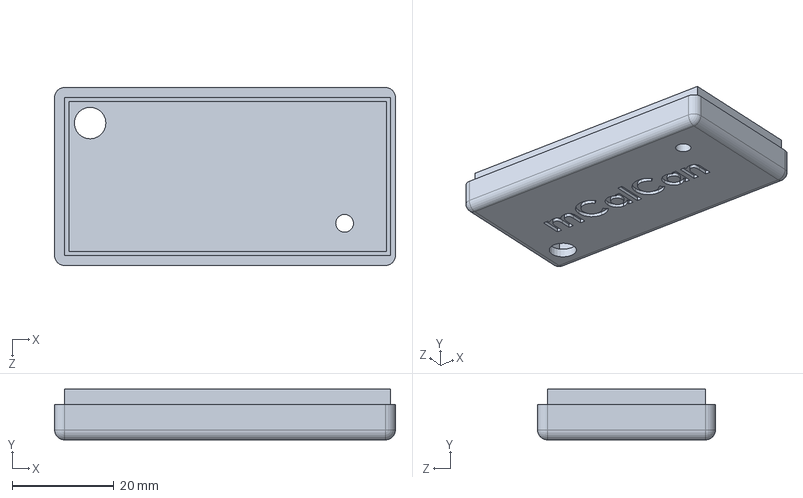
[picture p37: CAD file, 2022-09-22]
3D models/estacion terrena/Carcasa ET arriba.SLDPRT
67.0 x 10.0 x 35.0 mm

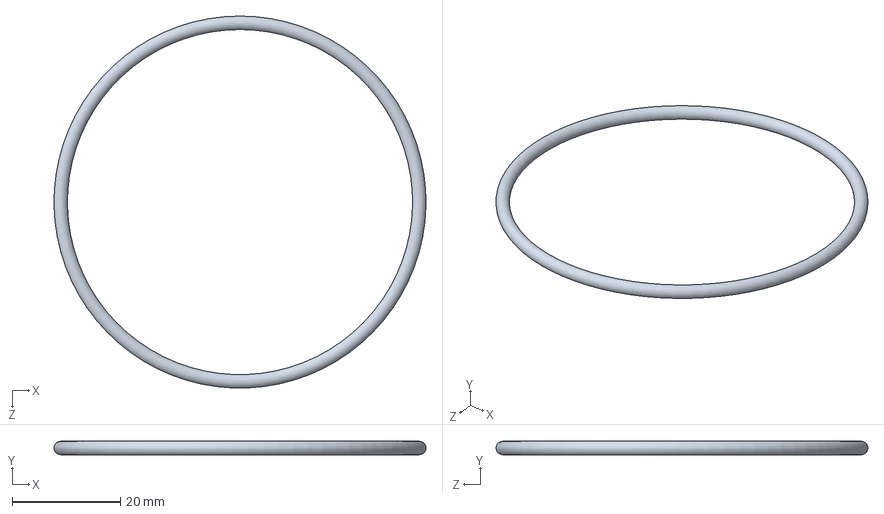
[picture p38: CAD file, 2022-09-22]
3D models/mCalCan/orrin.SLDPRT
68.8 x 2.50 x 68.8 mm

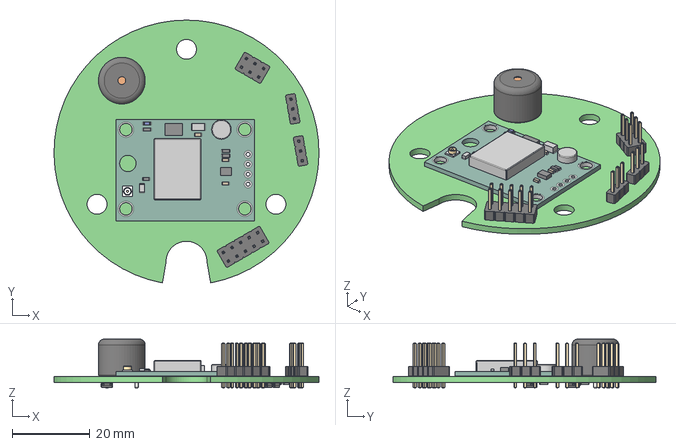
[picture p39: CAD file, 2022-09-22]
3D models/mCalCan/PCB/PCB4.step
68.0 x 67.4 x 12.5 mm
_autosave-PCB5 PCB

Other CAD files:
3D models/STL/soporte bateria V2.STL
sch/mCALCAN_lib.3d/ITG-MPU.STEP
3D models/Estacion Terrena v2/TapaInferior.SLDPRT
3D models/STL/Carcasa0,4.STL
3D models/Estacion Terrena v2/STL/TapaInferior.STL
3D models/Estacion Terrena v2/STLink.step
3D models/Estacion Terrena v2/TP4056.step
3D models/Estacion Terrena v2/USBHub.step
3D models/Estacion Terrena v2/sw.SLDPRT
3D models/STL/Carcasa ET abajo.STL
3D models/STL/Carcasa ET arriba.STL
3D models/STL/Carcasa superior.STL
3D models/STL/Carcasa.SLDPRT
3D models/STL/Carcasa.STL
3D models/STL/Corta separadores.STL
3D models/STL/Separador5.STL
3D models/STL/Soporte cargadores.STL
3D models/STL/TAPA INFERIOR.STL
3D models/STL/TAPA SUPERIOR huecos.STL
3D models/STL/TAPA SUPERIOR.STL
3D models/STL/VARILLA.STL
3D models/STL/estabilizador.STL
3D models/STL/polea.SLDPRT
3D models/STL/polea.STL
3D models/STL/soporte bateria.STL
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

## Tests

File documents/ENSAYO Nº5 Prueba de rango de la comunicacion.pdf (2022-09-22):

## ENSAYO N°5: Proyecto Mcalcan

Autor: Equipo G.V.I.E

Objeto: Comprobar el alcance de la transmisión inalámbrica LoRa

En este ensayo, queremos experimentar con el alcance de la transmisión inalámbrica de datos desde nuestra carga útil (CANSAT) hacia nuestra estación terrena para asegúranos de que dicho rango sea el necesario para cumplir nuestra misión.

Condiciones del ensayo:

- Protocolo de comunicación: Radio LoRa.
- Tamaño de bytes a transmitir: 100 bytes.
- Tasa de refresco [ms]: 500 ms.
- Entorno de pruebas: urbano.

Resultados del ensayo:

- Alcance de la transmisión inalámbrica: Utilizamos dos vehículos, uno con la estación terrena y el restante con el CANSAT. Tuvimos recibiendo datos fluidamente dentro del rango de 600m. Pasando de ese rango tenemos interferencias y se corta la señal.

Conclusión:

Luego de realizar esta prueba concluimos que el alcance de nuestra transmisión inalámbrica de datos mediante el protocolo LoRa es mas que suficiente para poder realizar la misión ya que la misma no supera esta altura.

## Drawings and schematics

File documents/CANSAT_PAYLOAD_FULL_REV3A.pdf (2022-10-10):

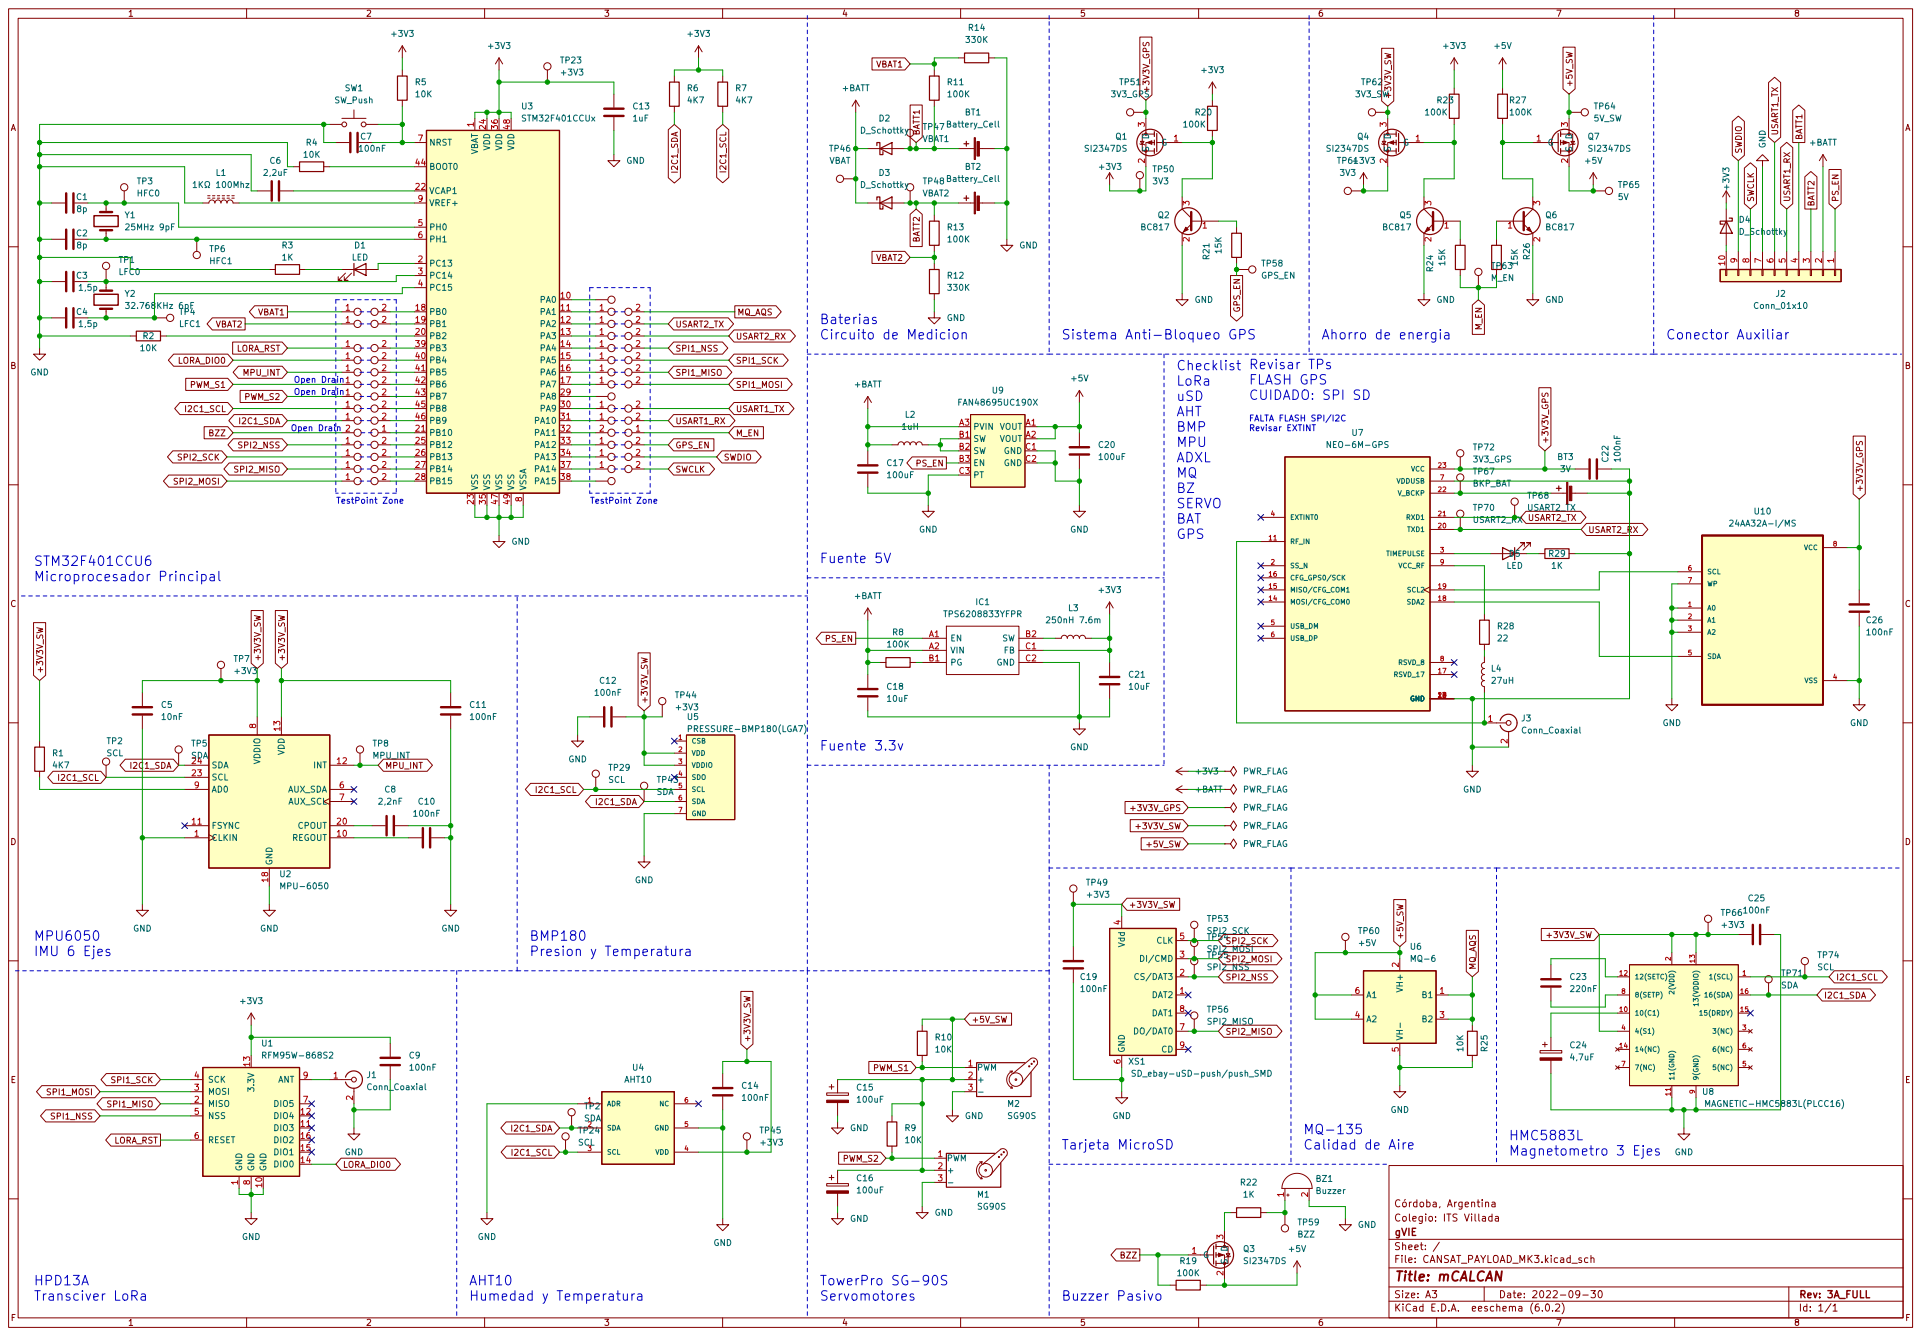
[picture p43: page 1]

1 PA0 10 PA1 11 PA2 12 PA3 13 PA4 14 PA5 15 PA6 16 PA7 17 PB0 18 PB1 19 PC13 2 PB2 20 PB10 21 VCAP1 22 VSS 23 VDD 24 PB12 25 PB13 26 PB14 27 PB15 28 PA8 29 PC14 3 PA9 30 PA10 31 PA11 32 PA12 33 PA13 34 VSS 35 VDD 36 PA14 37 PA15 38 PB3 39 PC15 4 PB4 40 PB5 41 PB6 42 PB7 43 BOOT0 44 PB8 45 PB9 46 VSS 47 VDD 48 VSS 49 PH0 5 PH1 6 NRST 7 VSSA

Revisar EXTINT Revisar TPs
FLASH GPS
CUIDADO: SPI SD

6 DO/DAT0 7 DAT1 8 CD 9 XS1SD_ebay-uSD-push/push_SMD

1 GND 10 DIO3 11 DIO4 12 3.3V 13 DIO0 14 DIO1 15 DIO2 16 MISO 2 MOSI 3 SCK 4 NSS 5 RESET 6 DIO5 7 GND

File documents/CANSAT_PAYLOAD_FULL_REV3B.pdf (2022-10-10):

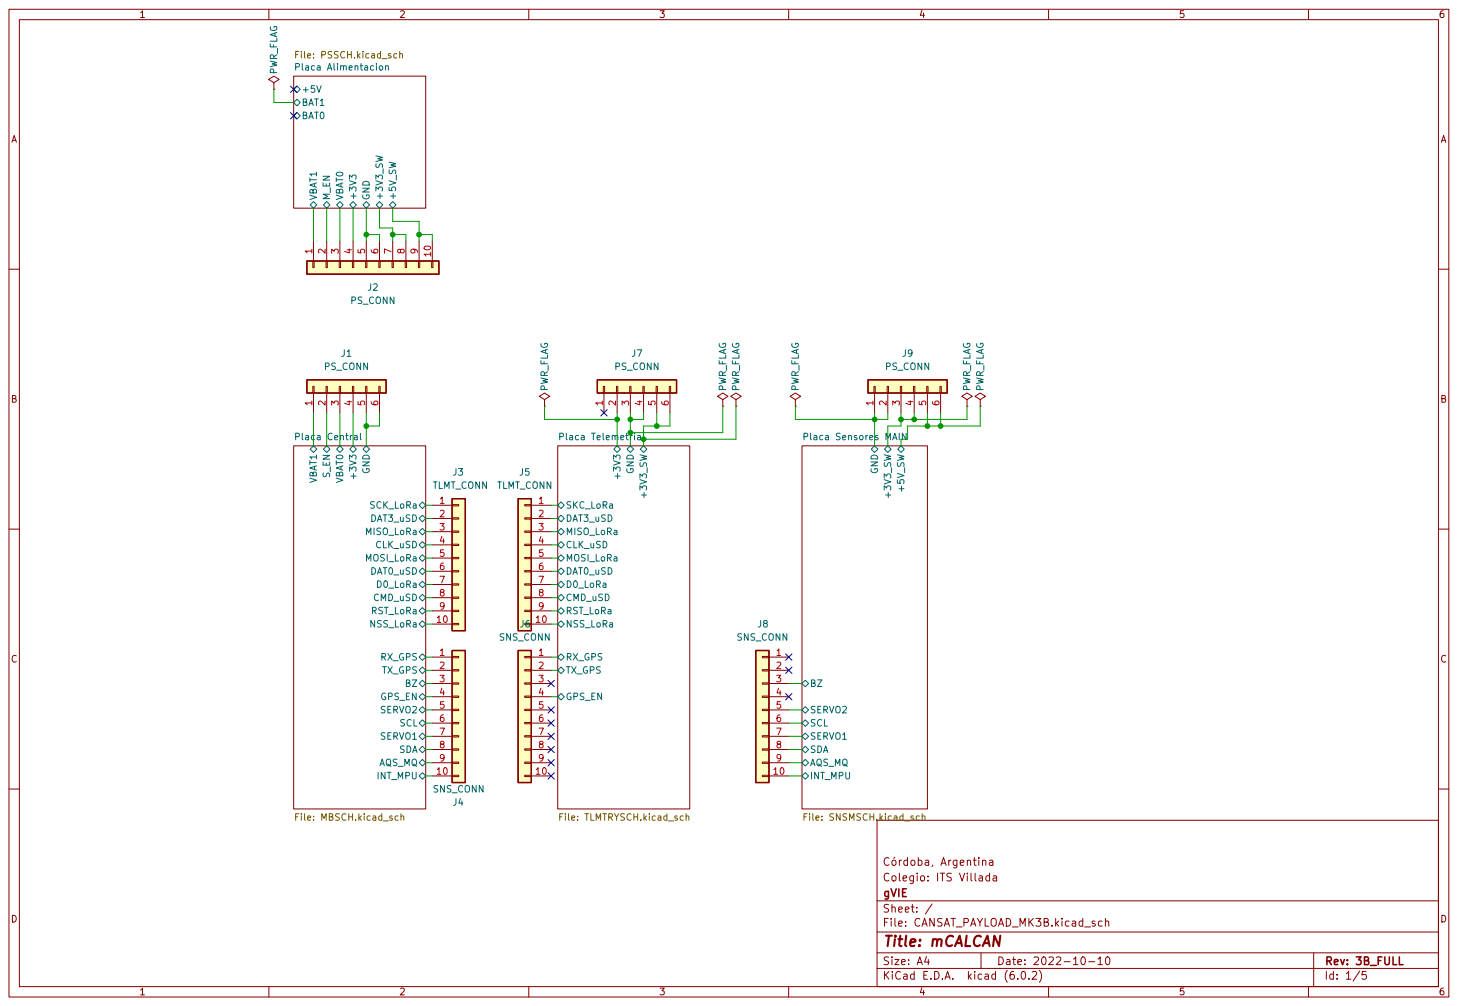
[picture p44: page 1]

SERVO2 SERVO1 BZ Placa Sensores MAIN

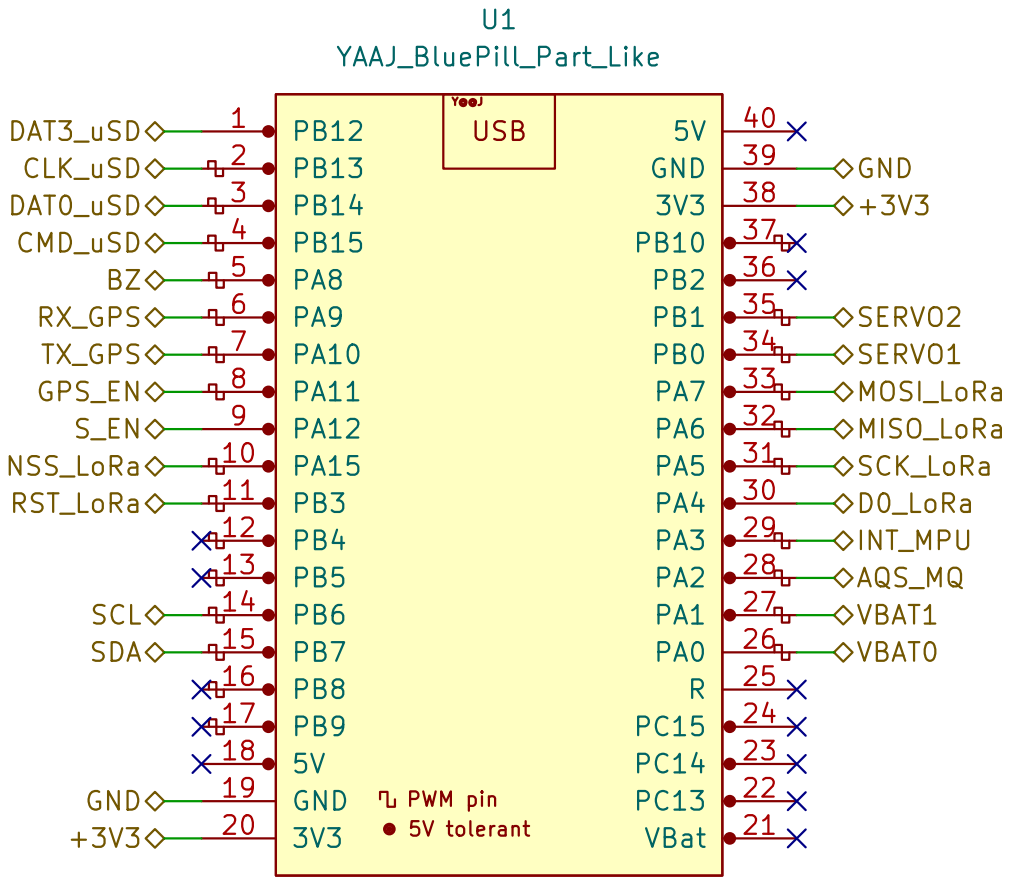
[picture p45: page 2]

Colegio: ITS Villada
File: MBSCH.kicad_sch Sheet: /Placa Central/ gVIE

Id: 2/5 Title: mCALCAN: Placa Central

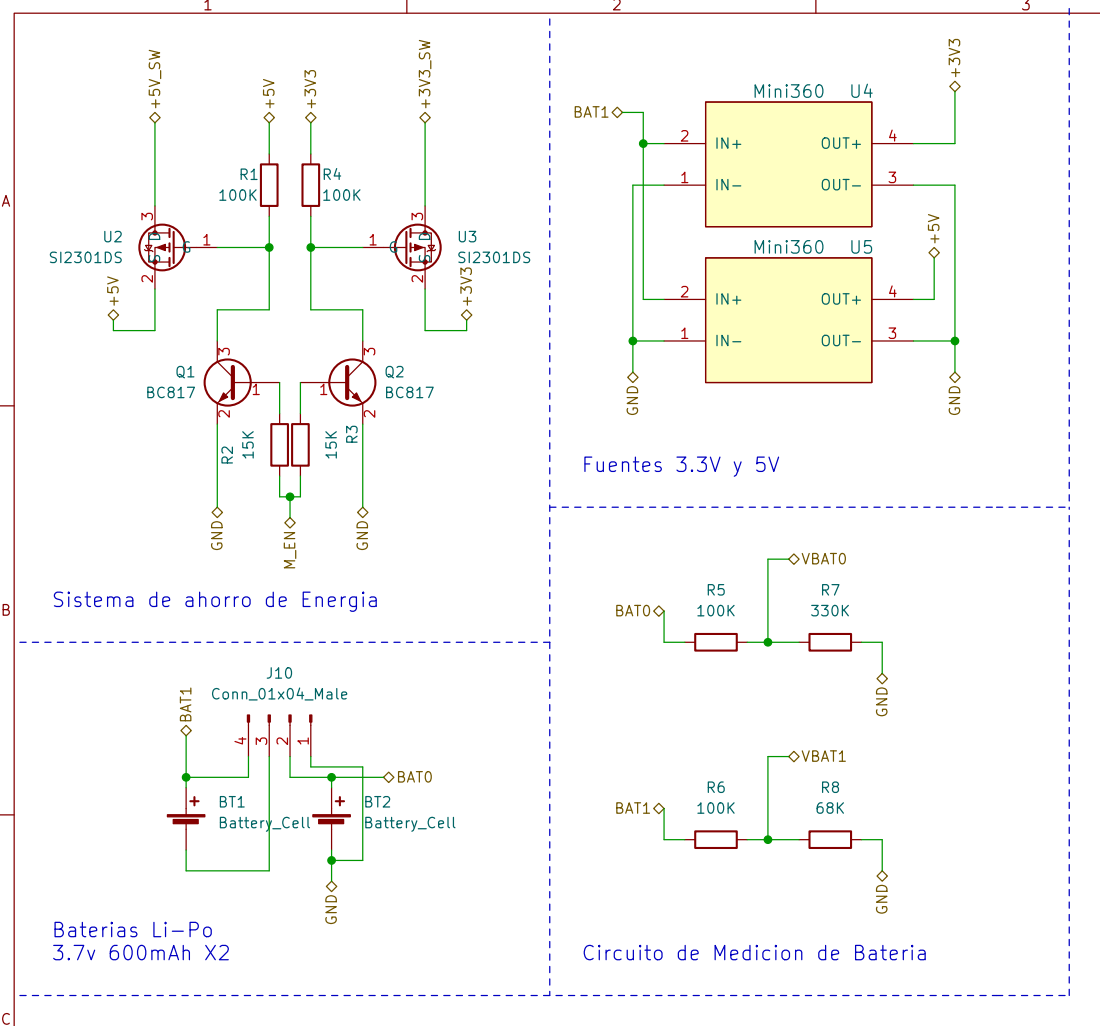
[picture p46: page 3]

Sistema de ahorro de Energia

Circuito de Medicion de Bateria

Colegio: ITS Villada
File: PSSCH.kicad_sch Sheet: /Placa Alimentacion/ gVIE

Id: 3/5 Title: mCALCAN: Placa Alimentacion

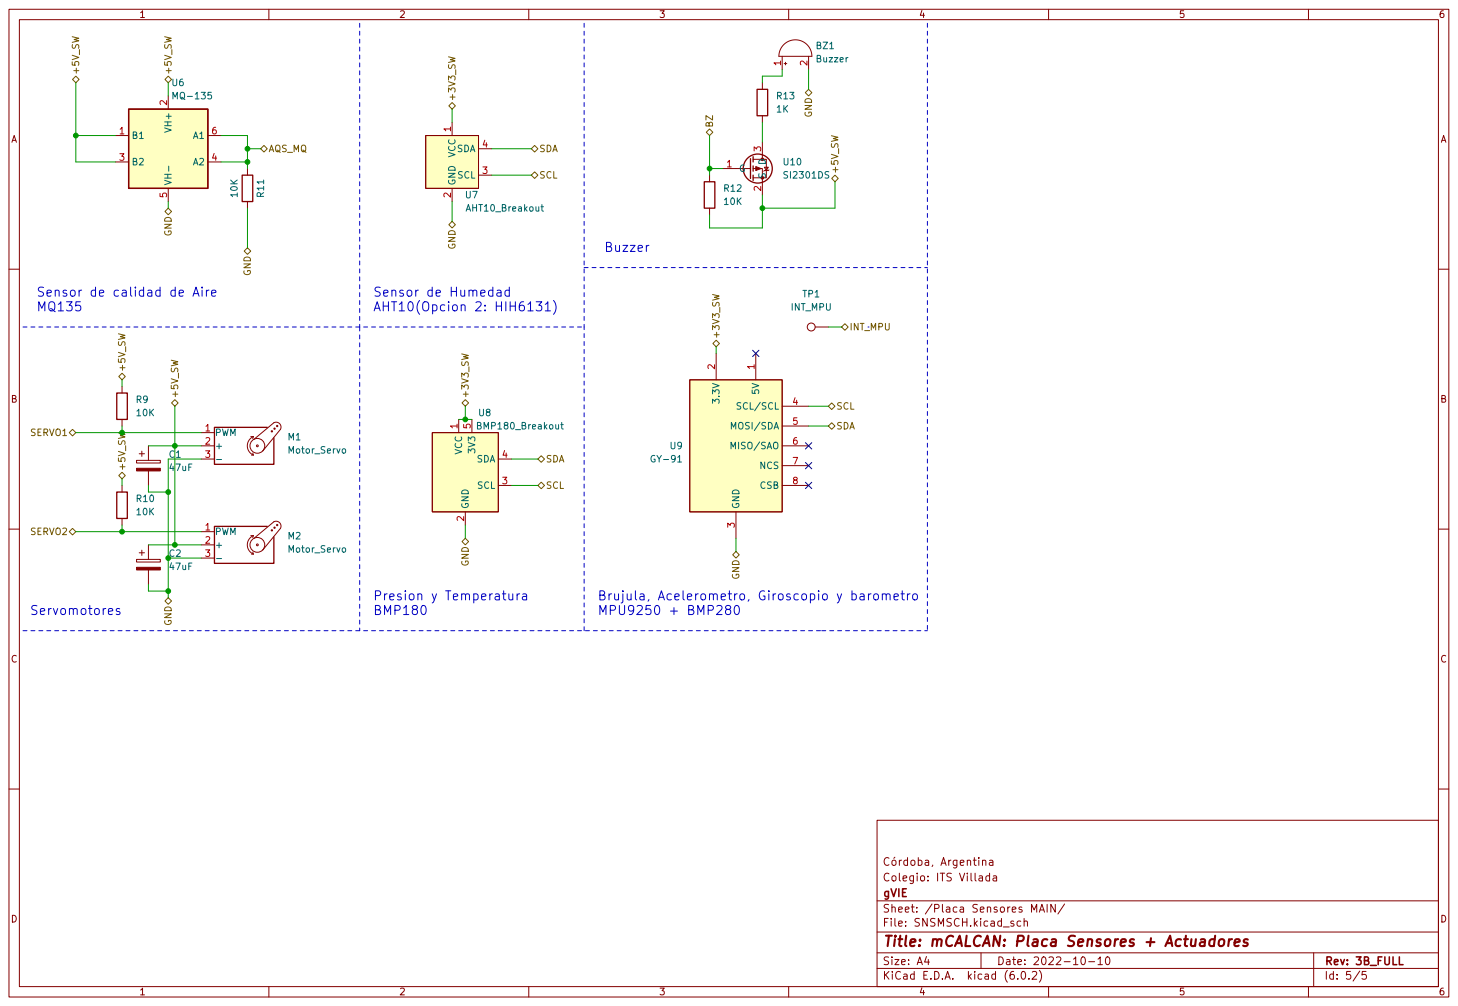
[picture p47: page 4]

3 SCL/SCL 4 MOSI/SDA 5 MISO/SAO 6 NCS 7 CSB 8 U9 GY-91 SCL GND

Sensor de calidad de Aire

Brujula, Acelerometro, Giroscopio y barometro
MPU9250 + BMP280

Colegio: ITS Villada
File: SNSMSCH.kicad_sch Sheet: /Placa Sensores MAIN/ gVIE

Id: 5/5 Title: mCALCAN: Placa Sensores + Actuadores

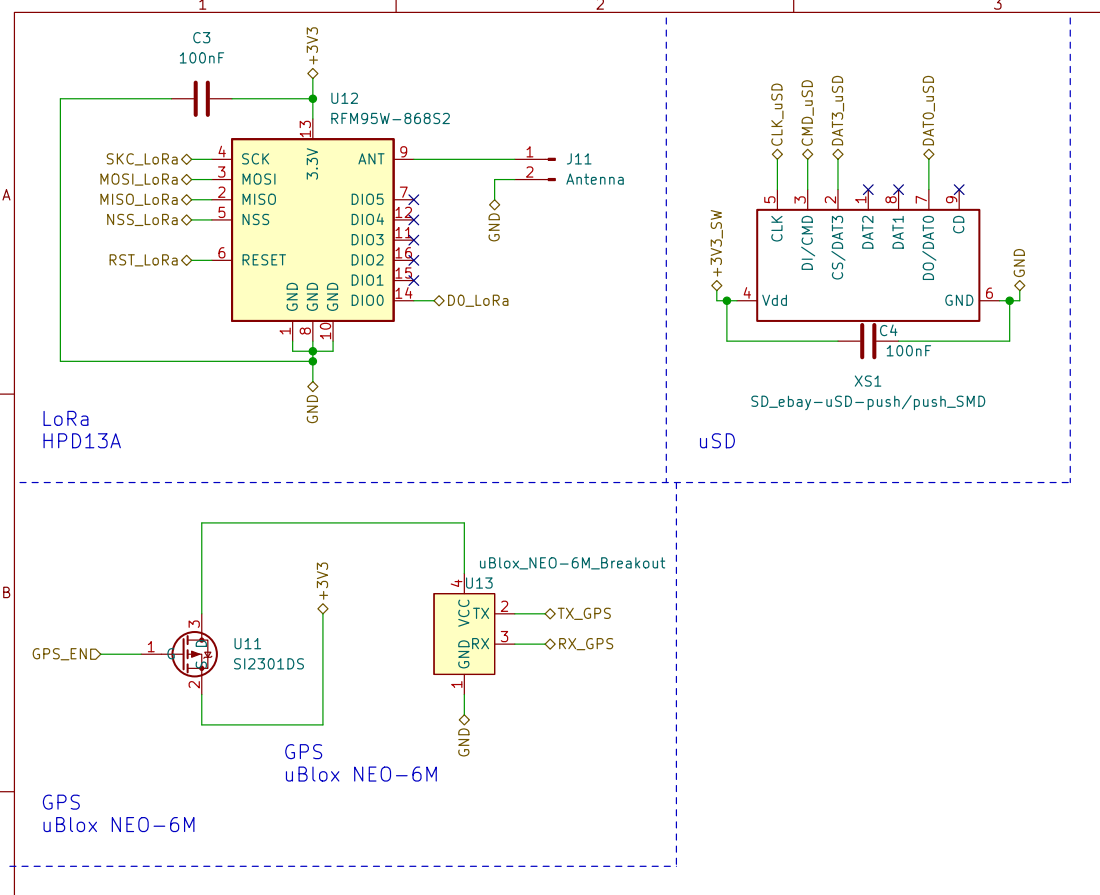
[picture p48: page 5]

1 GND 10 DIO3 11 DIO4 12 3.3V 13 DIO0 14 DIO1 15 DIO2 16 MISO 2 MOSI 3 SCK 4 NSS 5 RESET 6 DIO5 7 GND

Colegio: ITS Villada
File: TLMTRYSCH.kicad_sch Sheet: /Placa Telemetria/ gVIE

Id: 7/5 Title: mCALCAN: Placa Telemetria + GPS

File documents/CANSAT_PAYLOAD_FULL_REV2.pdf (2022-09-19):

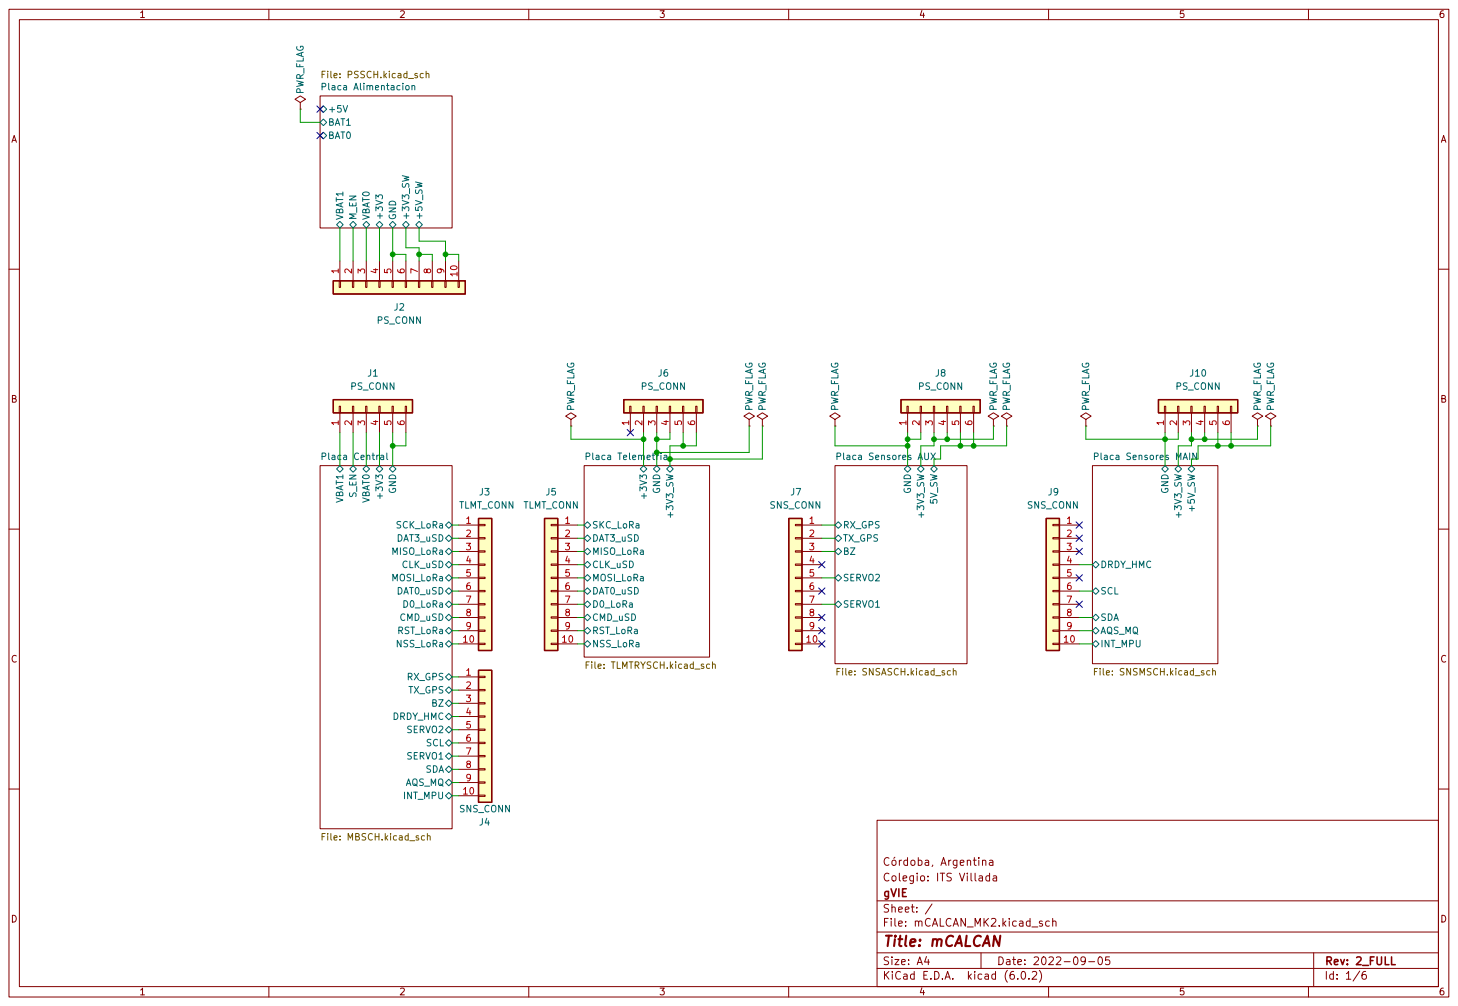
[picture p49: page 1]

Placa Telemetria File: TLMTRYSCH.kicad_sch CMD_uSD

BZ Placa Sensores AUX

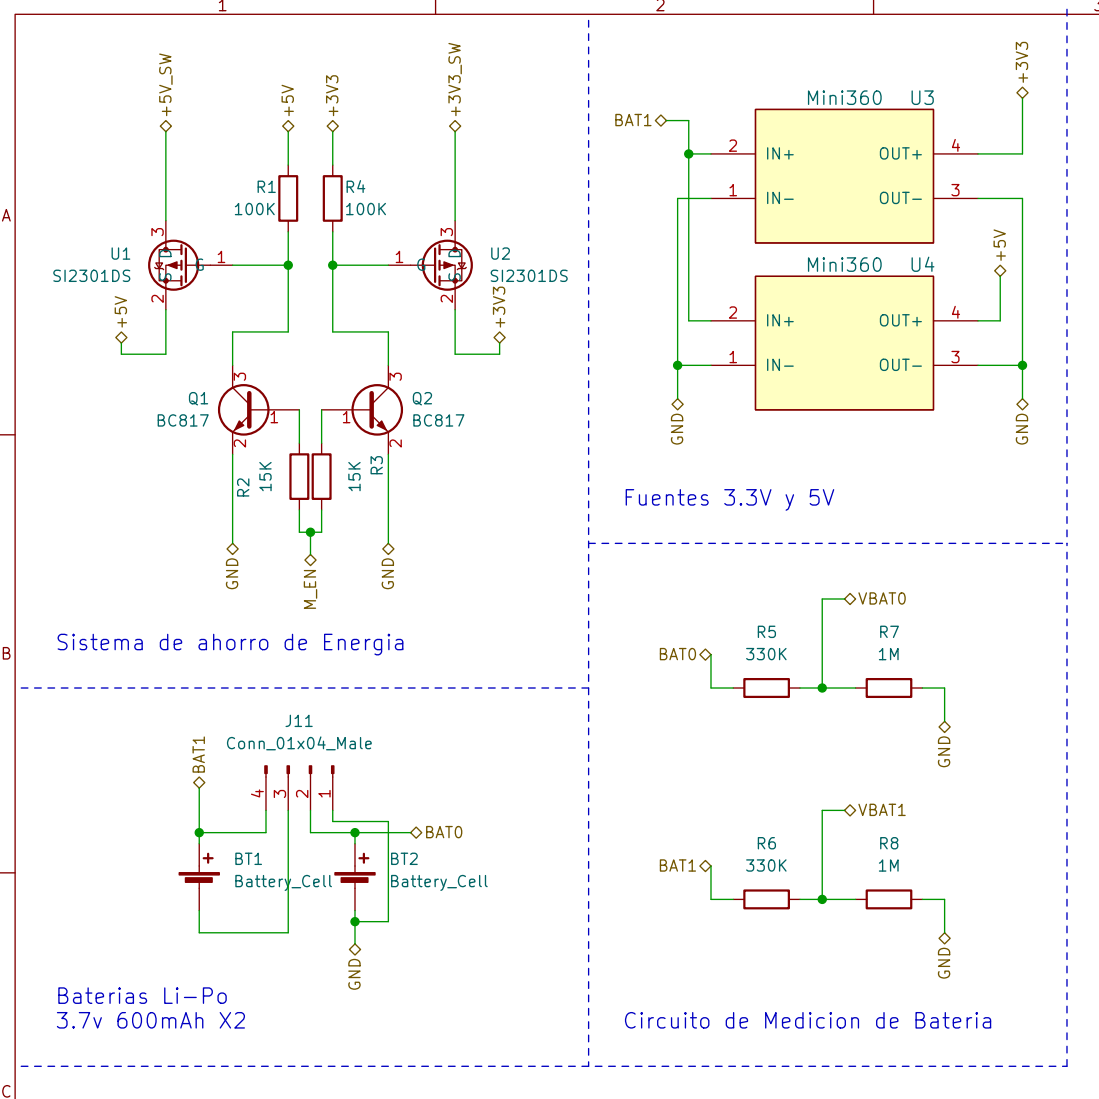
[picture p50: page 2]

Sistema de ahorro de Energia

Circuito de Medicion de Bateria

Colegio: ITS Villada
File: PSSCH.kicad_sch Sheet: /Placa Alimentacion/ gVIE

Id: 2/6 Title: mCALCAN: Placa Alimentacion

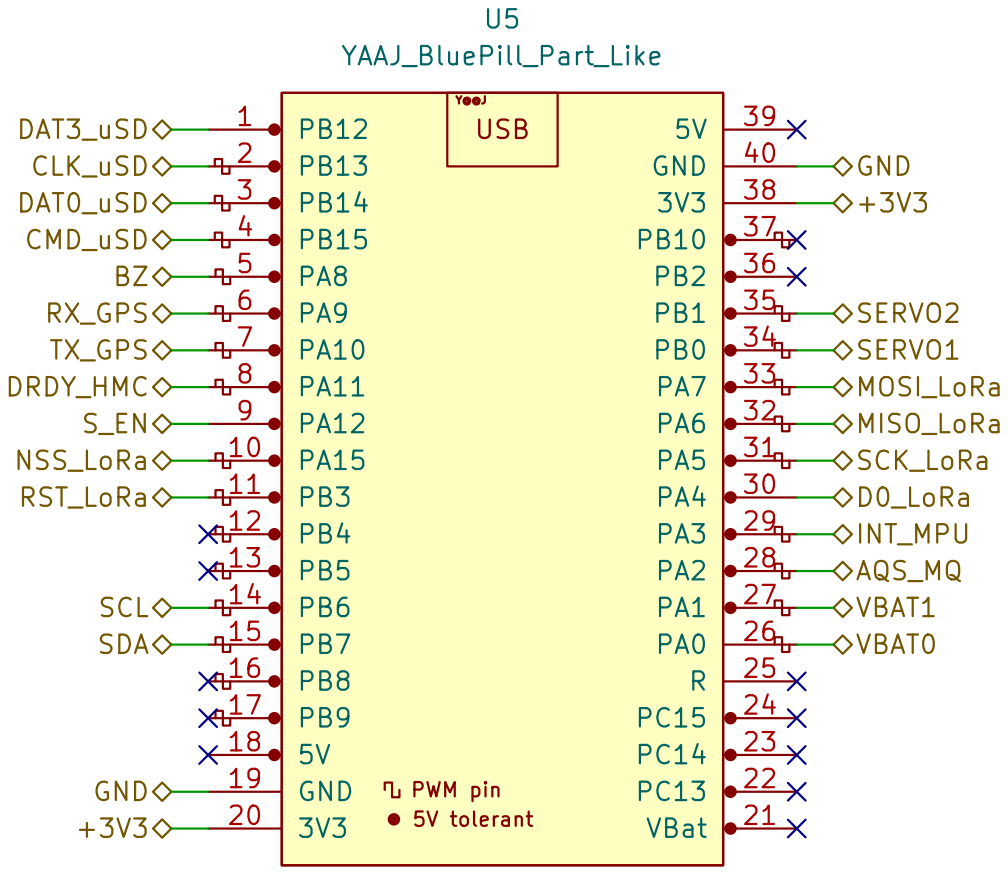
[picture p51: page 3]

Colegio: ITS Villada
File: MBSCH.kicad_sch Sheet: /Placa Central/ gVIE

Id: 3/6 Title: mCALCAN: Placa Central

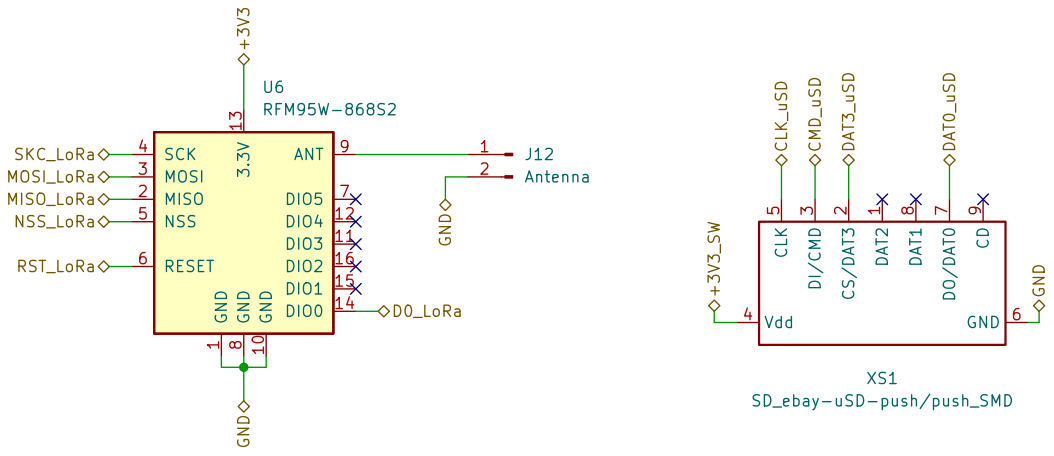
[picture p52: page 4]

1 GND 10 DIO3 11 DIO4 12 3.3V 13 DIO0 14 DIO1 15 DIO2 16 MISO 2 MOSI 3 SCK 4 NSS 5 RESET 6 DIO5 7 GND

Colegio: ITS Villada
File: TLMTRYSCH.kicad_sch Sheet: /Placa Telemetria/ gVIE

Id: 4/6 Title: mCALCAN: Placa Telemetria

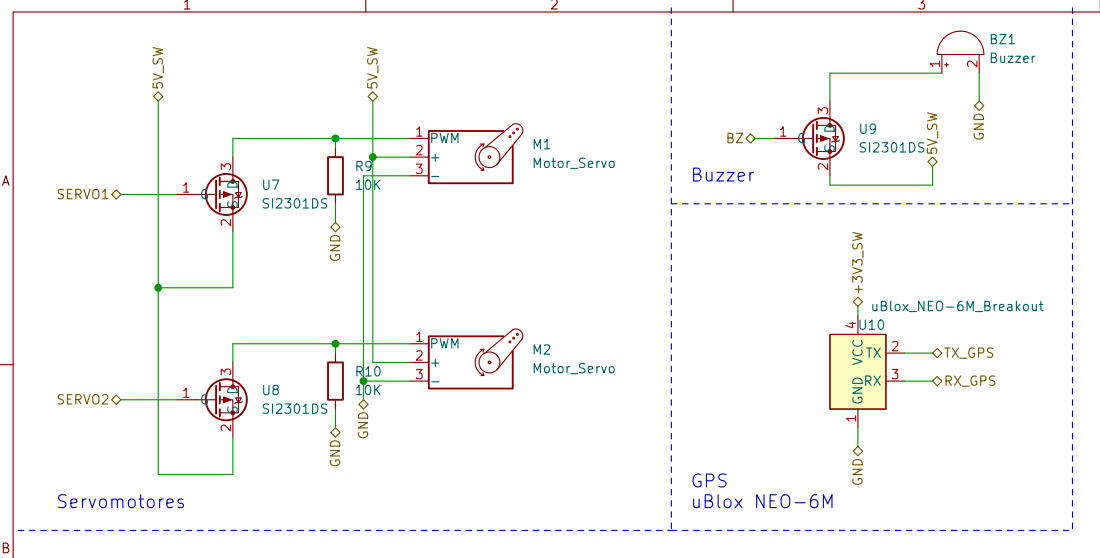
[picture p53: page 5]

Colegio: ITS Villada
File: SNSASCH.kicad_sch Sheet: /Placa Sensores AUX/ gVIE

Id: 5/6 Title: mCALCAN: Placa Sensores AUX

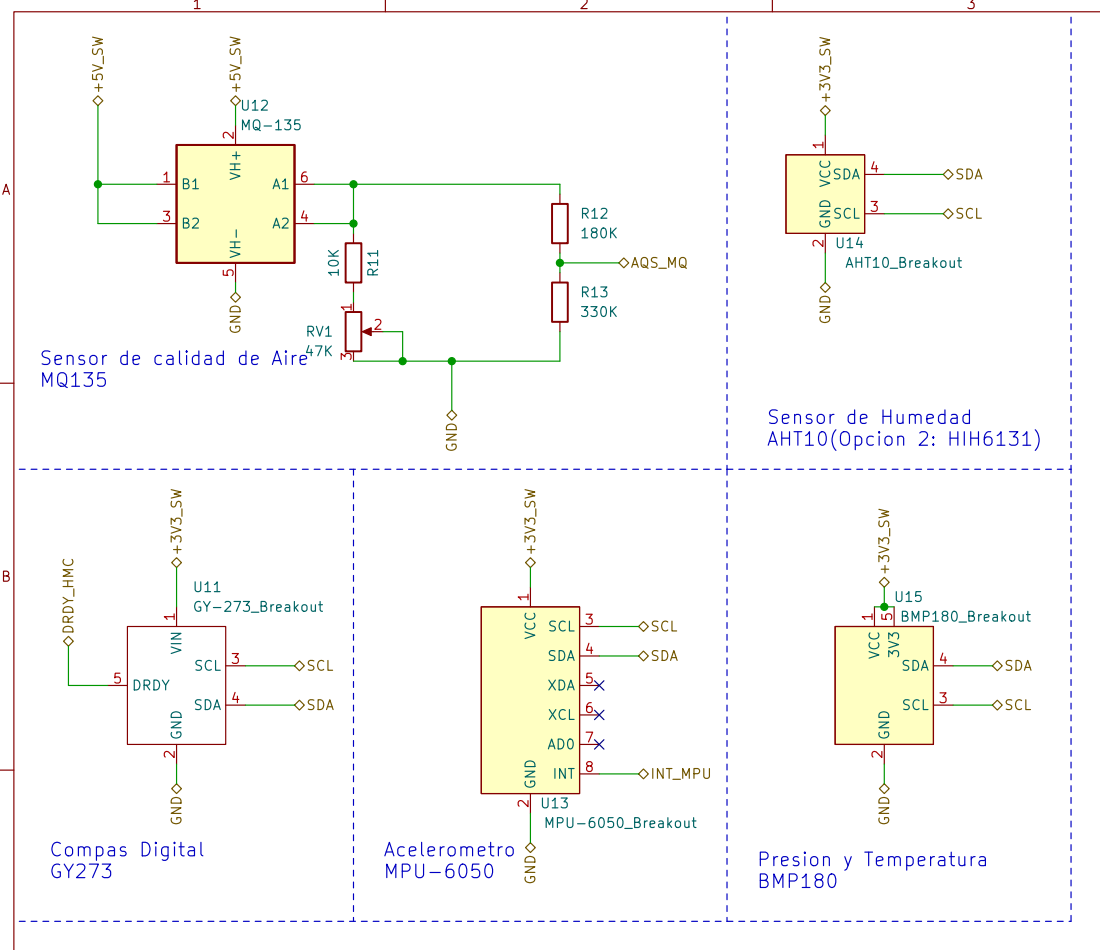
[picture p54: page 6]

SCL SCL GND GND +5V_SW

2 SCL 3 SDA 4 DRDY 5 U11 GY-273_Breakout B1 1 VH+

Sensor de calidad de Aire

2 SCL 3 SDA 4 XDA 5 XCL 6 AD0 7

Colegio: ITS Villada
File: SNSMSCH.kicad_sch Sheet: /Placa Sensores MAIN/ gVIE

Id: 6/6 Title: mCALCAN: Placa Sensores MAIN

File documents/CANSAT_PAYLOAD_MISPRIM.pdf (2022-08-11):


Circuito de Medicion de Bateria GNDGND

Acelerometro MPU-6050

Presion y Temperatura BMP180

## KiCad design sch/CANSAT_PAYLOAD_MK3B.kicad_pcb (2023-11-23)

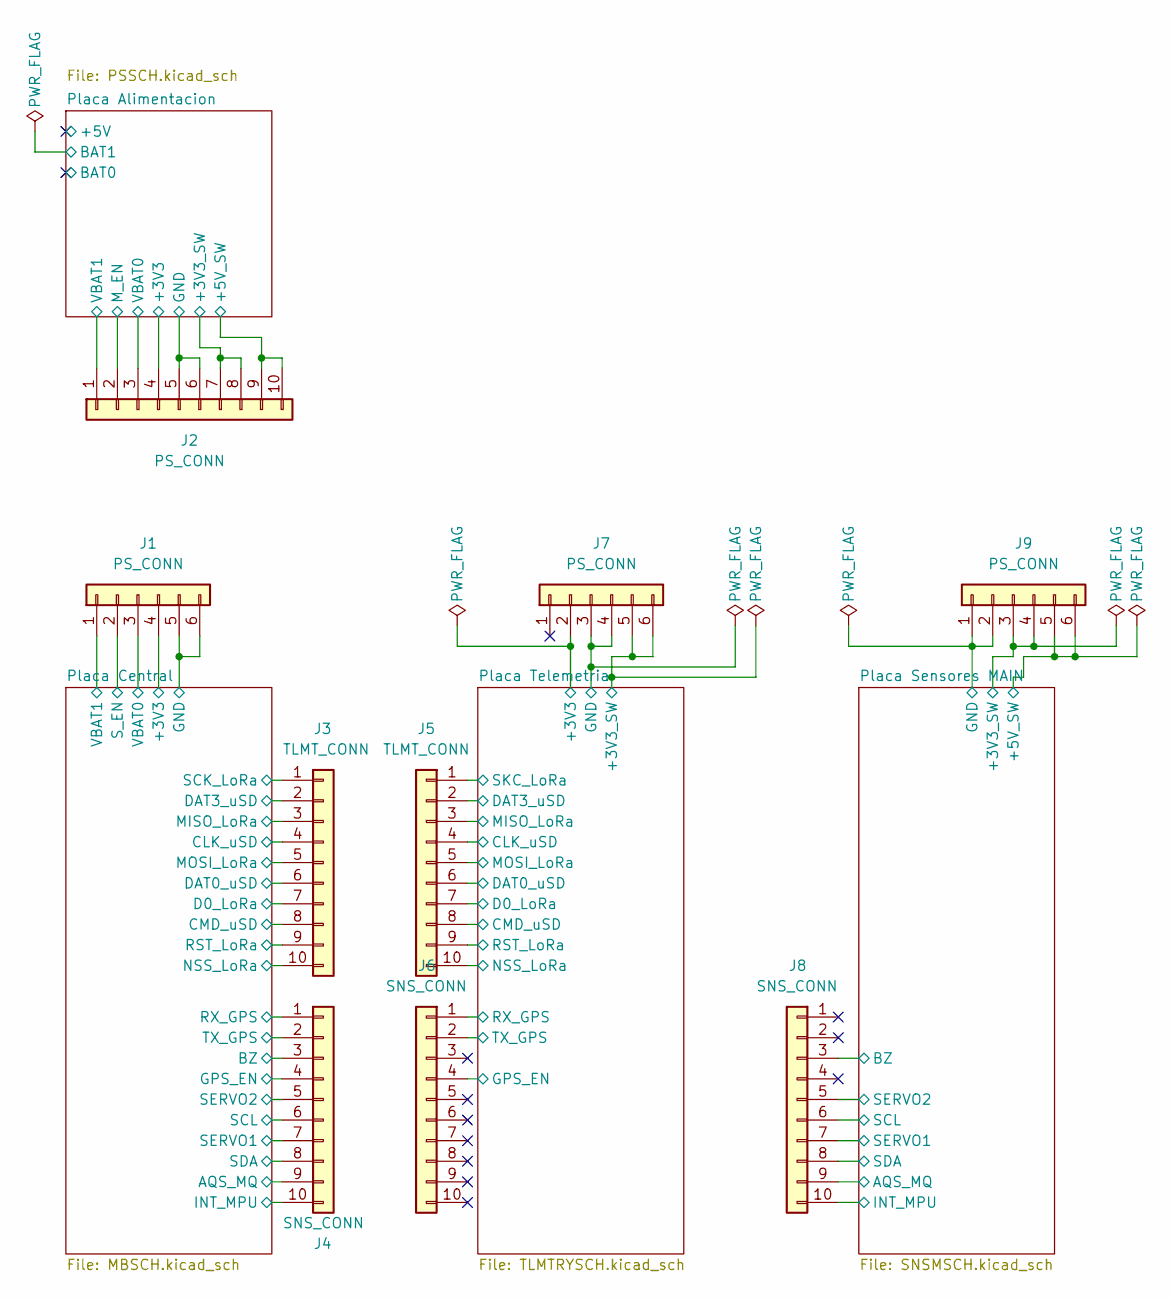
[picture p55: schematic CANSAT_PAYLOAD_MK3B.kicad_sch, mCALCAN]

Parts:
J1, J7, J9: PS_CONN; PCB_CONN_S
J2: PS_CONN; PCB_CONN
J3, J5: TLMT_CONN; PCB_CONN
J4, J6, J8: SNS_CONN; PCB_CONN

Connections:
/Placa Alimentacion/+3V3: J2.4; also elsewhere on the board
/Placa Alimentacion/+3V3_SW: J2.7, J2.8; also elsewhere on the board
/Placa Alimentacion/+5V_SW: J2.9, J2.10; also elsewhere on the board
/Placa Alimentacion/GND: J2.5, J2.6; also elsewhere on the board
/Placa Alimentacion/M_EN: J2.2; also elsewhere on the board
/Placa Alimentacion/VBAT0: J2.3; also elsewhere on the board
/Placa Alimentacion/VBAT1: J2.1; also elsewhere on the board
/Placa Central/+3V3: J1.4; also elsewhere on the board
/Placa Central/AQS_MQ: J4.9; also elsewhere on the board
/Placa Central/BZ: J4.3; also elsewhere on the board
/Placa Central/CLK_uSD: J3.4; also elsewhere on the board
/Placa Central/CMD_uSD: J3.8; also elsewhere on the board
/Placa Central/D0_LoRa: J3.7; also elsewhere on the board
/Placa Central/DAT0_uSD: J3.6; also elsewhere on the board
/Placa Central/DAT3_uSD: J3.2; also elsewhere on the board
/Placa Central/GND: J1.5, J1.6; also elsewhere on the board
/Placa Central/GPS_EN: J4.4; also elsewhere on the board
/Placa Central/INT_MPU: J4.10; also elsewhere on the board
/Placa Central/MISO_LoRa: J3.3; also elsewhere on the board
/Placa Central/MOSI_LoRa: J3.5; also elsewhere on the board
/Placa Central/NSS_LoRa: J3.10; also elsewhere on the board
/Placa Central/RST_LoRa: J3.9; also elsewhere on the board
/Placa Central/RX_GPS: J4.1; also elsewhere on the board
/Placa Central/SCK_LoRa: J3.1; also elsewhere on the board
/Placa Central/SCL: J4.6; also elsewhere on the board
/Placa Central/SDA: J4.8; also elsewhere on the board
/Placa Central/SERVO1: J4.7; also elsewhere on the board
/Placa Central/SERVO2: J4.5; also elsewhere on the board
/Placa Central/S_EN: J1.2; also elsewhere on the board
/Placa Central/TX_GPS: J4.2; also elsewhere on the board
/Placa Central/VBAT0: J1.3; also elsewhere on the board
/Placa Central/VBAT1: J1.1; also elsewhere on the board
/Placa Sensores MAIN/+3V3_SW: J9.3, J9.4; also elsewhere on the board
/Placa Sensores MAIN/+5V_SW: J9.5, J9.6; also elsewhere on the board
/Placa Sensores MAIN/AQS_MQ: J8.9; also elsewhere on the board
/Placa Sensores MAIN/BZ: J8.3; also elsewhere on the board
/Placa Sensores MAIN/GND: J9.1, J9.2; also elsewhere on the board
/Placa Sensores MAIN/INT_MPU: J8.10; also elsewhere on the board
/Placa Sensores MAIN/SCL: J8.6; also elsewhere on the board
/Placa Sensores MAIN/SDA: J8.8; also elsewhere on the board
/Placa Sensores MAIN/SERVO1: J8.7; also elsewhere on the board
/Placa Sensores MAIN/SERVO2: J8.5; also elsewhere on the board
/Placa Telemetria/+3V3: J7.2; also elsewhere on the board
/Placa Telemetria/+3V3_SW: J7.5, J7.6; also elsewhere on the board
/Placa Telemetria/CLK_uSD: J5.4; also elsewhere on the board
/Placa Telemetria/CMD_uSD: J5.8; also elsewhere on the board
/Placa Telemetria/D0_LoRa: J5.7; also elsewhere on the board
/Placa Telemetria/DAT0_uSD: J5.6; also elsewhere on the board
/Placa Telemetria/DAT3_uSD: J5.2; also elsewhere on the board
/Placa Telemetria/GND: J7.3, J7.4; also elsewhere on the board
/Placa Telemetria/GPS_EN: J6.4; also elsewhere on the board
/Placa Telemetria/MISO_LoRa: J5.3; also elsewhere on the board
/Placa Telemetria/MOSI_LoRa: J5.5; also elsewhere on the board
/Placa Telemetria/NSS_LoRa: J5.10; also elsewhere on the board
/Placa Telemetria/RST_LoRa: J5.9; also elsewhere on the board
/Placa Telemetria/RX_GPS: J6.1; also elsewhere on the board
/Placa Telemetria/SKC_LoRa: J5.1; also elsewhere on the board
/Placa Telemetria/TX_GPS: J6.2; also elsewhere on the board

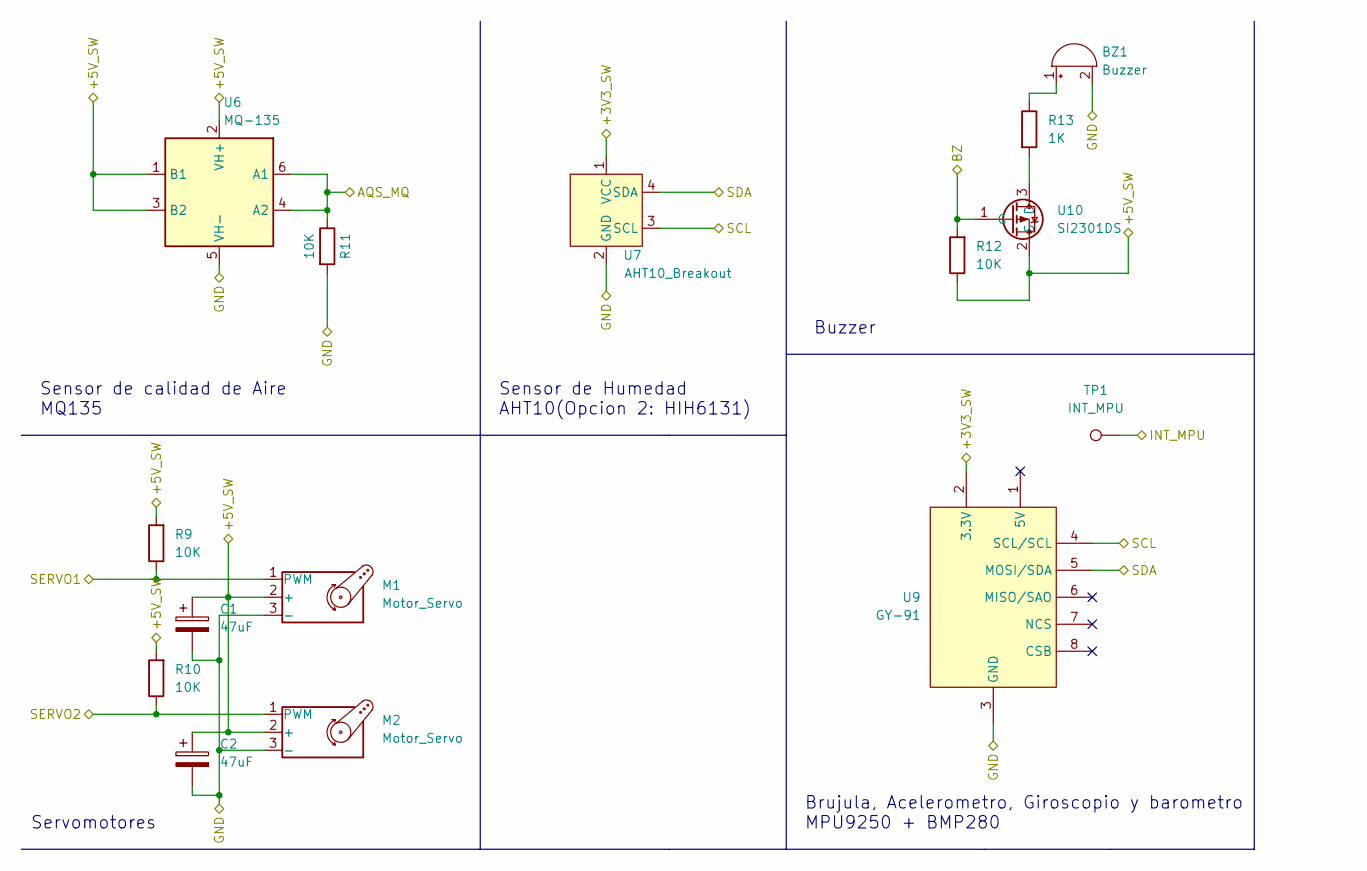
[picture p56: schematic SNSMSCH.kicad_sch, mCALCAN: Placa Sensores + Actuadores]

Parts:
BZ1: Buzzer; Buzzer_12x9.5RM7.6
C1, C2: 47uF; CP_Elec_4x5.3
M1, M2: Motor_Servo; PinHeader_1x03_P2.54mm_Vertical
R9, R10, R11, R12: 10K; R_0805_2012Metric_Pad1.20x1.40mm_HandSolder
R13: 1K; R_0805_2012Metric_Pad1.20x1.40mm_HandSolder
TP1: INT_MPU; TestPoint_THTPad_D1.5mm_Drill0.7mm
U6: MQ-135; MQ-6
U7: AHT10_Breakout
U9: GY-91; GY-91_Breakout
U10: SI2301DS; SOT-23

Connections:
/Placa Sensores MAIN/+3V3_SW: U7.1 (VCC), U9.2 (3.3V); also elsewhere on the board
/Placa Sensores MAIN/+5V_SW: C1.1, C2.1, M1.2 (+), M2.2 (+), R9.2, R10.2, R12.1, U6.1 (B1), U6.2 (VH+), U6.3 (B2), U10.2 (S); also elsewhere on the board
/Placa Sensores MAIN/AQS_MQ: R11.1, U6.4 (A2), U6.6 (A1); also elsewhere on the board
/Placa Sensores MAIN/BZ: R12.2, U10.1 (G); also elsewhere on the board
/Placa Sensores MAIN/GND: BZ1.2 (+), C1.2, C2.2, M1.3 (-), M2.3 (-), R11.2, U6.5 (VH-), U7.2 (GND), U9.3 (GND); also elsewhere on the board
/Placa Sensores MAIN/INT_MPU: TP1.1; also elsewhere on the board
/Placa Sensores MAIN/SCL: U7.3 (SCL), U9.4 (SCL/SCL); also elsewhere on the board
/Placa Sensores MAIN/SDA: U7.4 (SDA), U9.5 (MOSI/SDA); also elsewhere on the board
/Placa Sensores MAIN/SERVO1: M1.1 (PWM), R9.1; also elsewhere on the board
/Placa Sensores MAIN/SERVO2: M2.1 (PWM), R10.1; also elsewhere on the board
unnamed: BZ1.1 (-), R13.1
unnamed: R13.2, U10.3 (D)

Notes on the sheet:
Buzzer
Sensor de Humedad AHT10(Opcion 2: HIH6131)
Brujula, Acelerometro, Giroscopio y barometro MPU9250 + BMP280
Sensor de calidad de Aire MQ135
Servomotores

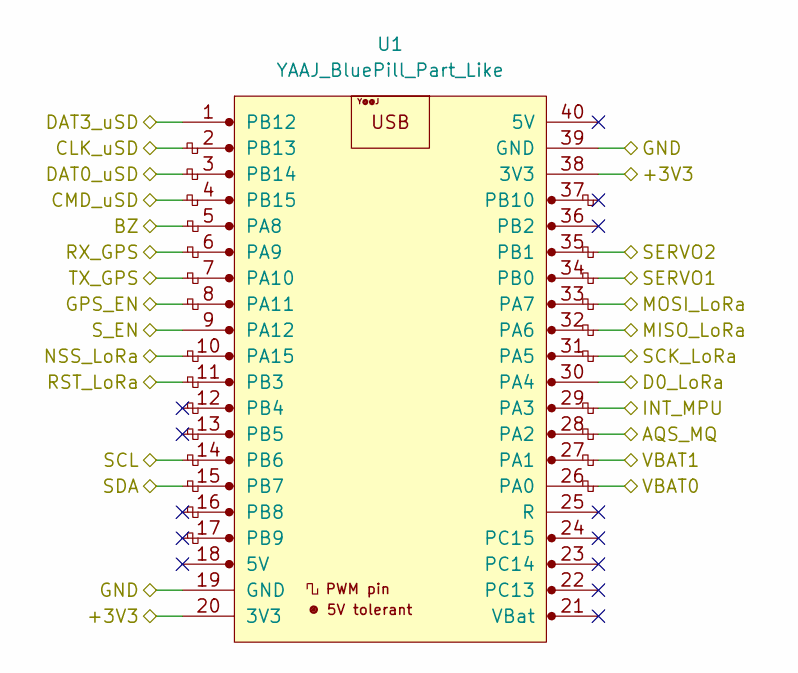
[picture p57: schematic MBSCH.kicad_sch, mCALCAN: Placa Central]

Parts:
U1: YAAJ_BluePill_Part_Like; YAAJ_BluePill_2

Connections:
/Placa Central/+3V3: U1.20 (3V3), U1.38 (3V3); also elsewhere on the board
/Placa Central/AQS_MQ: U1.28 (PA2); also elsewhere on the board
/Placa Central/BZ: U1.5 (PA8); also elsewhere on the board
/Placa Central/CLK_uSD: U1.2 (PB13); also elsewhere on the board
/Placa Central/CMD_uSD: U1.4 (PB15); also elsewhere on the board
/Placa Central/D0_LoRa: U1.30 (PA4); also elsewhere on the board
/Placa Central/DAT0_uSD: U1.3 (PB14); also elsewhere on the board
/Placa Central/DAT3_uSD: U1.1 (PB12); also elsewhere on the board
/Placa Central/GND: U1.19 (GND), U1.39 (GND); also elsewhere on the board
/Placa Central/GPS_EN: U1.8 (PA11); also elsewhere on the board
/Placa Central/INT_MPU: U1.29 (PA3); also elsewhere on the board
/Placa Central/MISO_LoRa: U1.32 (PA6); also elsewhere on the board
/Placa Central/MOSI_LoRa: U1.33 (PA7); also elsewhere on the board
/Placa Central/NSS_LoRa: U1.10 (PA15); also elsewhere on the board
/Placa Central/RST_LoRa: U1.11 (PB3); also elsewhere on the board
/Placa Central/RX_GPS: U1.6 (PA9); also elsewhere on the board
/Placa Central/SCK_LoRa: U1.31 (PA5); also elsewhere on the board
/Placa Central/SCL: U1.14 (PB6); also elsewhere on the board
/Placa Central/SDA: U1.15 (PB7); also elsewhere on the board
/Placa Central/SERVO1: U1.34 (PB0); also elsewhere on the board
/Placa Central/SERVO2: U1.35 (PB1); also elsewhere on the board
/Placa Central/S_EN: U1.9 (PA12); also elsewhere on the board
/Placa Central/TX_GPS: U1.7 (PA10); also elsewhere on the board
/Placa Central/VBAT0: U1.26 (PA0); also elsewhere on the board
/Placa Central/VBAT1: U1.27 (PA1); also elsewhere on the board

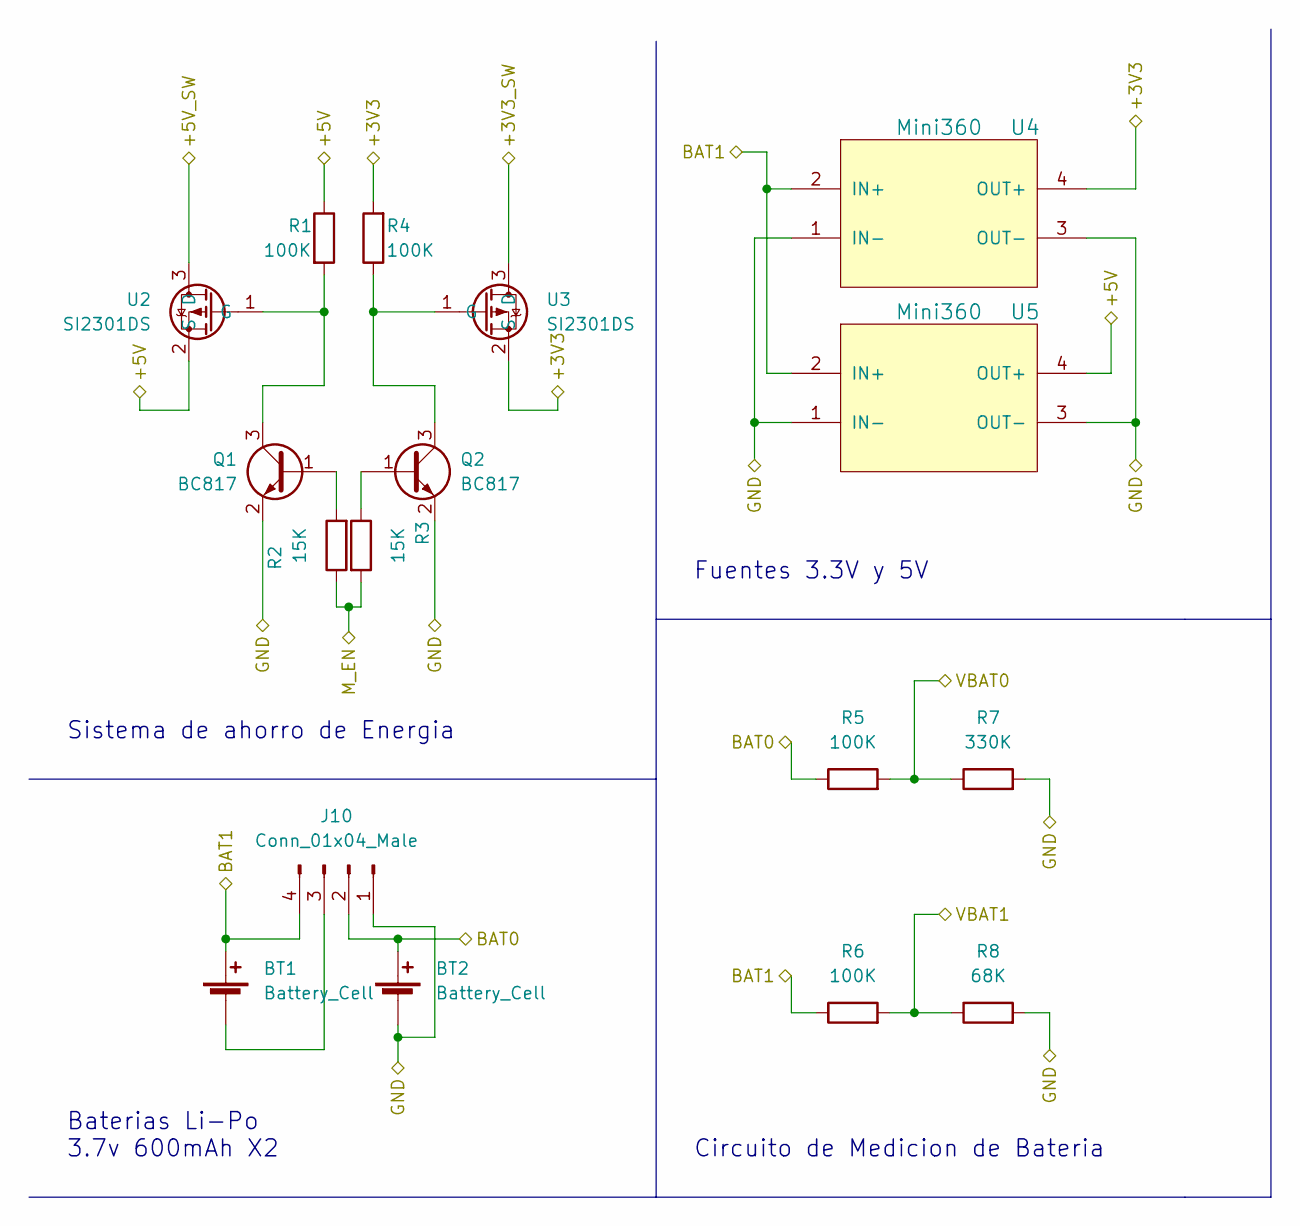
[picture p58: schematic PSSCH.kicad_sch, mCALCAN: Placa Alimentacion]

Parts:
BT1, BT2: Battery_Cell; Molex_Micro-Latch_53253-0270_1x02_P2.00mm_Vertical
J10: Conn_01x04_Male; PinHeader_1x04_P2.54mm_Vertical
Q1, Q2: BC817; SOT-23
R1, R4, R5, R6: 100K; R_0805_2012Metric_Pad1.20x1.40mm_HandSolder
R2, R3: 15K; R_0805_2012Metric_Pad1.20x1.40mm_HandSolder
R7: 330K; R_0805_2012Metric_Pad1.20x1.40mm_HandSolder
R8: 68K; R_0805_2012Metric_Pad1.20x1.40mm_HandSolder
U2, U3: SI2301DS; SOT-23
U4, U5: Mini360; Mini360_step-down

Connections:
/Placa Alimentacion/+3V3: R4.2, U3.2 (S), U4.4 (OUT+); also elsewhere on the board
/Placa Alimentacion/+3V3_SW: U3.3 (D); also elsewhere on the board
/Placa Alimentacion/+5V: R1.1, U2.2 (S), U5.4 (OUT+)
/Placa Alimentacion/+5V_SW: U2.3 (D); also elsewhere on the board
/Placa Alimentacion/BAT0: BT2.1 (+), J10.2, R5.1
/Placa Alimentacion/BAT1: BT1.1 (+), J10.4, R6.1, U4.2 (IN+), U5.2 (IN+)
/Placa Alimentacion/GND: BT2.2 (-), J10.1, Q1.2 (E), Q2.2 (E), R7.2, R8.2, U4.1 (IN-), U4.3 (OUT-), U5.1 (IN-), U5.3 (OUT-); also elsewhere on the board
/Placa Alimentacion/M_EN: R2.1, R3.2; also elsewhere on the board
/Placa Alimentacion/VBAT0: R5.2, R7.1; also elsewhere on the board
/Placa Alimentacion/VBAT1: R6.2, R8.1; also elsewhere on the board
unnamed: BT1.2 (-), J10.3
unnamed: Q1.1 (B), R2.2
unnamed: Q1.3 (C), R1.2, U2.1 (G)
unnamed: Q2.1 (B), R3.1
unnamed: Q2.3 (C), R4.1, U3.1 (G)

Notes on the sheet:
Baterias Li-Po 3.7v 600mAh X2
Sistema de ahorro de Energia
Fuentes 3.3V y 5V
Circuito de Medicion de Bateria

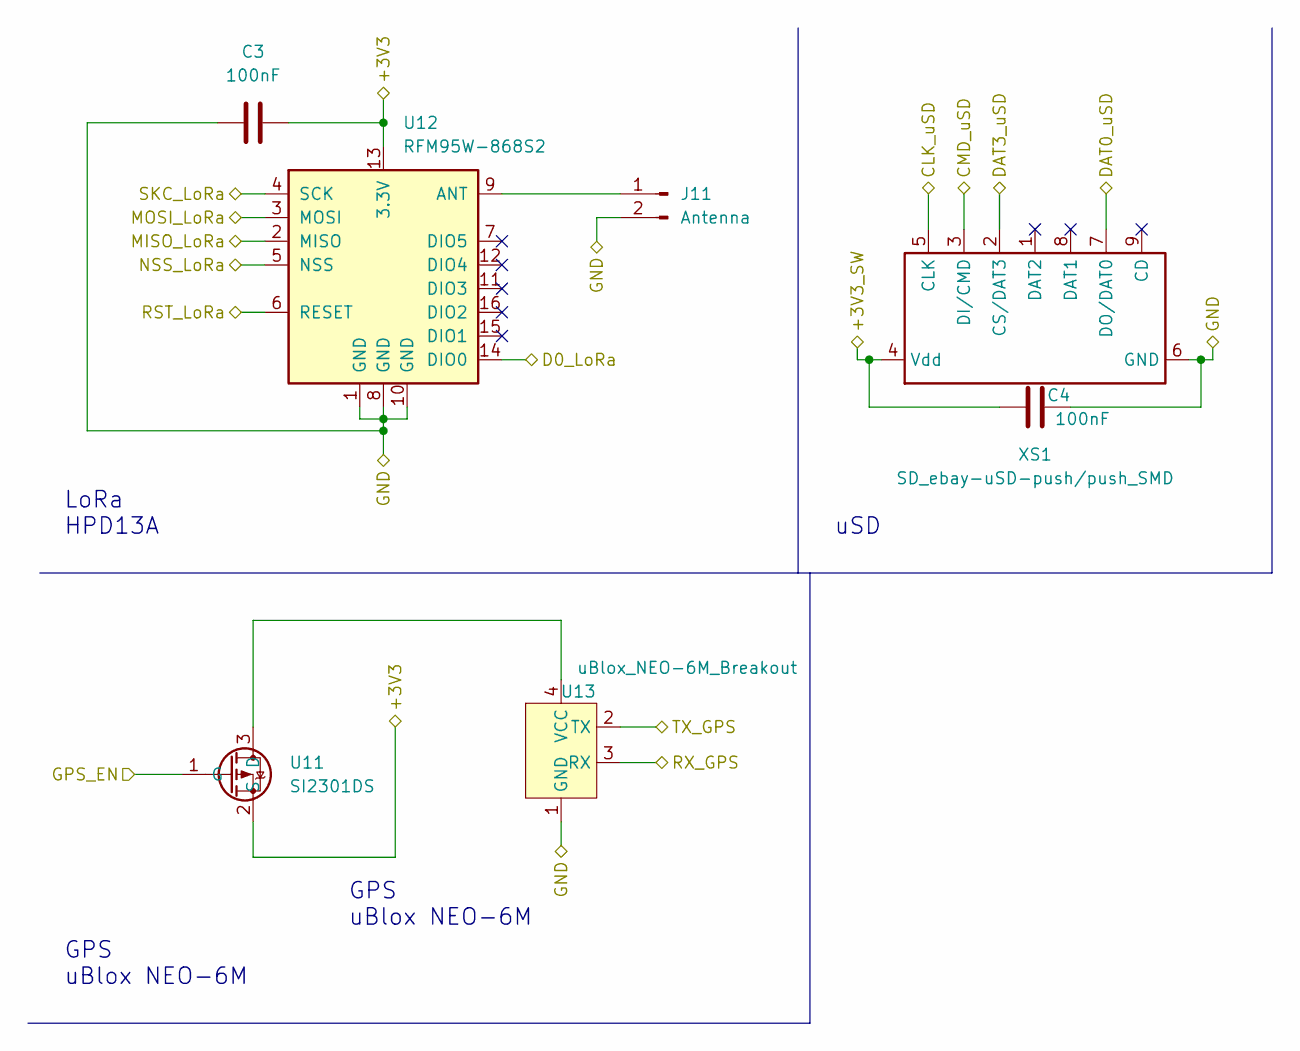
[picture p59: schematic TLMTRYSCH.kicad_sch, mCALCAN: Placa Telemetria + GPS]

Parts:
C3, C4: 100nF; C_0805_2012Metric_Pad1.18x1.45mm_HandSolder
J11: Antenna; U.FL_Molex_MCRF_73412-0110_Vertical
U11: SI2301DS; SOT-23
U12: RFM95W-868S2; HOPERF_RFM9XW_SMD
U13: uBlox_NEO-6M_Breakout; uBlox-NEO-6M_Breakout
XS1: SD_ebay-uSD-push/push_SMD; Conn_uSDcard

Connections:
/Placa Telemetria/+3V3: C3.2, U11.2 (S), U12.13 (3.3V); also elsewhere on the board
/Placa Telemetria/+3V3_SW: C4.1, XS1.4 (Vdd); also elsewhere on the board
/Placa Telemetria/CLK_uSD: XS1.5 (CLK); also elsewhere on the board
/Placa Telemetria/CMD_uSD: XS1.3 (DI/CMD); also elsewhere on the board
/Placa Telemetria/D0_LoRa: U12.14 (DIO0); also elsewhere on the board
/Placa Telemetria/DAT0_uSD: XS1.7 (DO/DAT0); also elsewhere on the board
/Placa Telemetria/DAT3_uSD: XS1.2 (CS/DAT3); also elsewhere on the board
/Placa Telemetria/GND: C3.1, C4.2, J11.2, U12.1 (GND), U12.8 (GND), U12.10 (GND), U13.1 (GND), XS1.6 (GND); also elsewhere on the board
/Placa Telemetria/GPS_EN: U11.1 (G); also elsewhere on the board
/Placa Telemetria/MISO_LoRa: U12.2 (MISO); also elsewhere on the board
/Placa Telemetria/MOSI_LoRa: U12.3 (MOSI); also elsewhere on the board
/Placa Telemetria/NSS_LoRa: U12.5 (NSS); also elsewhere on the board
/Placa Telemetria/RST_LoRa: U12.6 (RESET); also elsewhere on the board
/Placa Telemetria/RX_GPS: U13.3 (RX); also elsewhere on the board
/Placa Telemetria/SKC_LoRa: U12.4 (SCK); also elsewhere on the board
/Placa Telemetria/TX_GPS: U13.2 (TX); also elsewhere on the board
unnamed: J11.1, U12.9 (ANT)
unnamed: U11.3 (D), U13.4 (VCC)

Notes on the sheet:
GPS uBlox NEO-6M
LoRa HPD13A
uSD

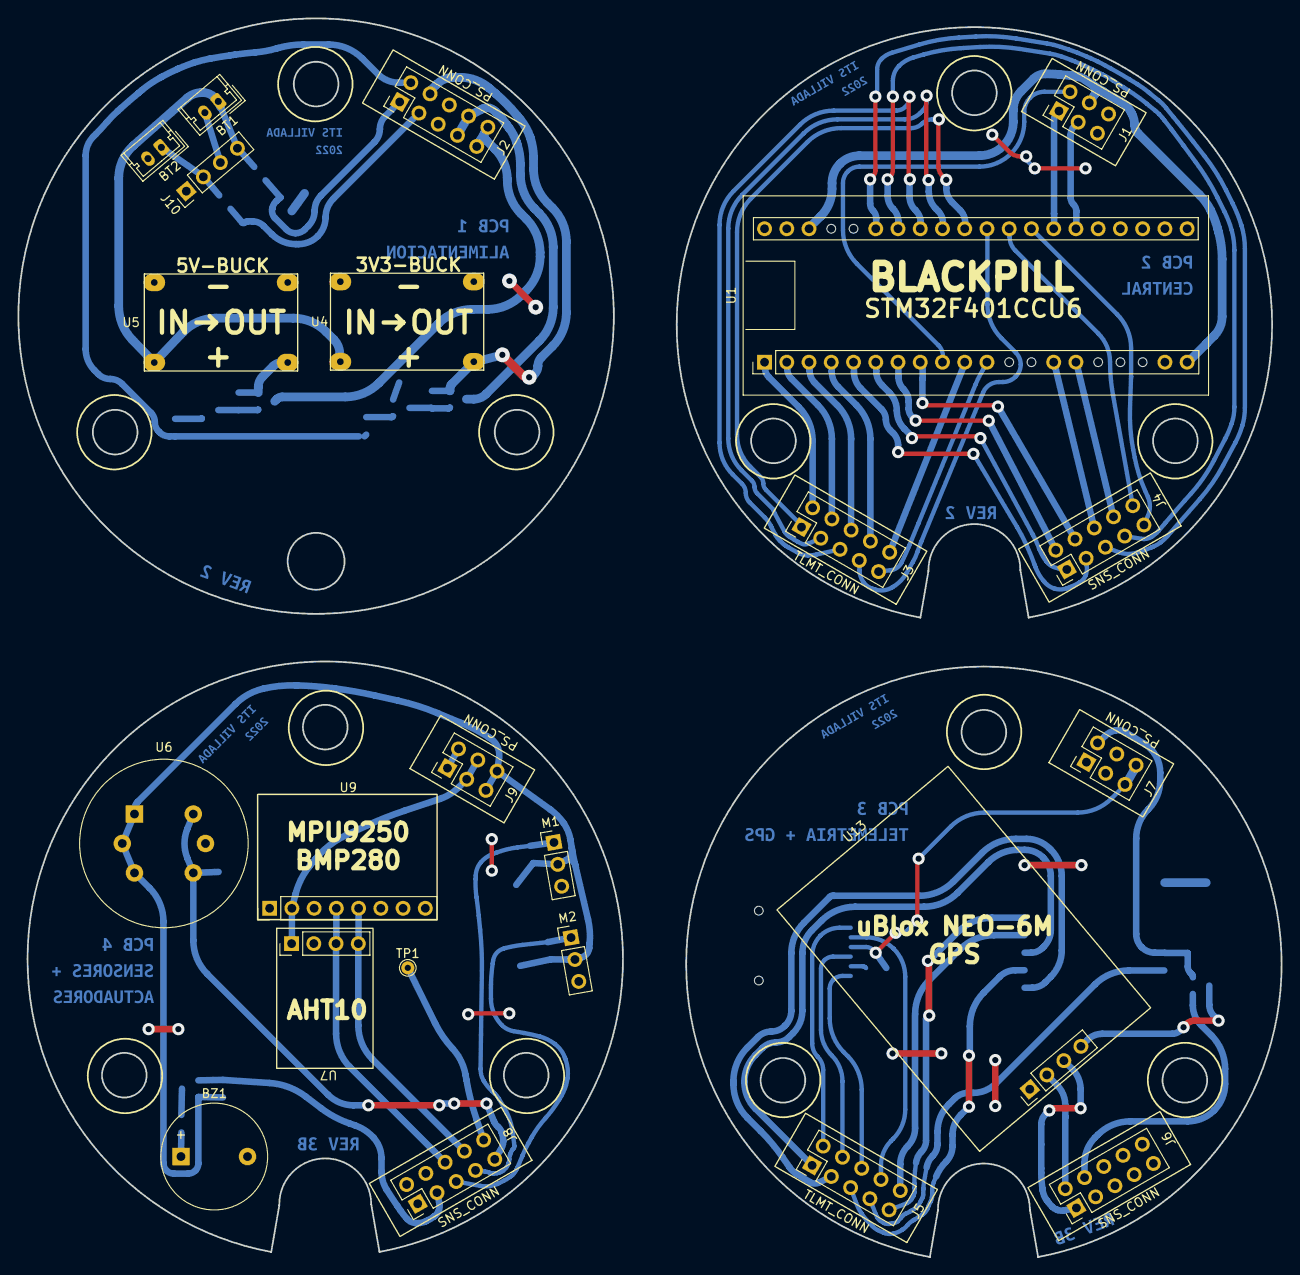
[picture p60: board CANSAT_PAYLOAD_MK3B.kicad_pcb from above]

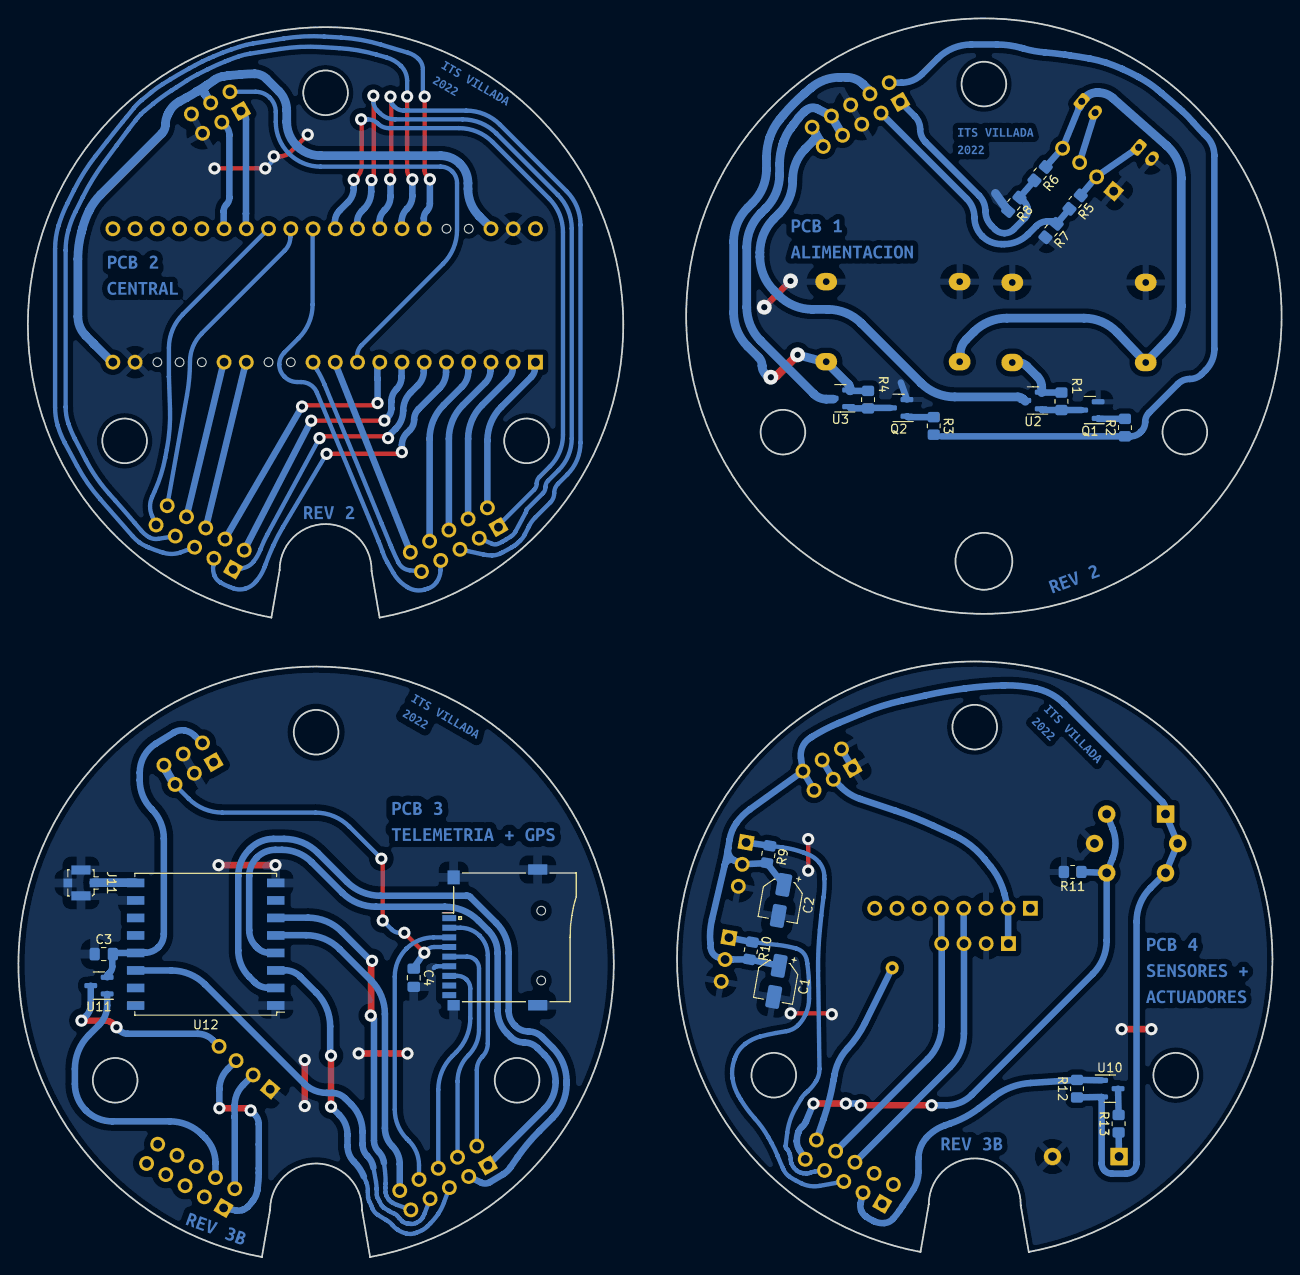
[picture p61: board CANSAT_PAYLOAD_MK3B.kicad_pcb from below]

Board: 2 copper layers, 144.3 x 141.5 mm, 61 parts (38 on the bottom side), 70 nets.

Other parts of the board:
kibuzzard-6319D247, kibuzzard-6319D247#2, kibuzzard-6319D247#3, kibuzzard-6319D247#4: G***; kibuzzard-6319D247
kibuzzard-6344A53A: G***; kibuzzard-6344A53A
kibuzzard-63173E9C: G***; kibuzzard-63173E9C
kibuzzard-63173EF4: G***; kibuzzard-63173EF4
kibuzzard-63447E72, kibuzzard-63447E72#2: G***; kibuzzard-63447E72
kibuzzard-63447E86: G***; kibuzzard-63447E86
kibuzzard-634739A2: G***; kibuzzard-634739A2
kibuzzard-634739B3: G***; kibuzzard-634739B3

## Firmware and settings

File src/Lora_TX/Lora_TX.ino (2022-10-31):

#include <TinyGPS++.h>
#include <TinyGPSPlus.h>
#include <AHTxx.h>
#include <EEPROM.h>
#include <LoRa.h>
#include <SPI.h>
#include <STM32TimerInterrupt.h>
#include <STM32_ISR_Timer.h>
#include <STM32_ISR_Timer.hpp>
#include <SD.h>
#include <Wire.h>
#include "MPU9250.h"
#include <Servo.h>
#include <BMP280_DEV.h>

#define GPS_BAUDRATE 115200L
#define LORA_FREQUENCY 915000000 // Frecuencia en Hz a la que se quiere transmitir.
#define LORA_SYNC_WORD 0xDE      // Byte value to use as the sync word, defaults to 0x12
#define LORA_POWER 19            // TX power in dB, defaults to 17. Supported values are 2 to 20 for PA_OUTPUT_PA_BOOST_PIN, and 0 to 14 for PA_OUTPUT_RFO_PIN.
#define LORA_SPREAD_FACTOR 7     // Spreading factor, defaults to 7. Supported values are between 6 and 12 (En Argentina se puede utilizar entre 7 a 10)
#define LORA_SIG_BANDWIDTH 125E3 // Signal bandwidth in Hz, defaults to 125E3. Supported values are 7.8E3, 10.4E3, 15. 6E3, 20.8E3, 31.25E3, 41.7E3, 62.5E3, 125E3, 250E3, and 500E3
#define LORA_CODING_RATE 5       // Denominator of the coding rate, defaults to 5. Supported values are between 5 and 8, these correspond to coding rates of 4/5 and 4/8. The coding rate numerator is fixed at 4.
#define RST PB3                  // Pin Reset del transciver LoRa
#define IRQ PA4                  // Pin DIO0 del transciver LoRa
#define NSS PA15                 // Pin CS del transciver LoRa
#define INTMPU PA3               // Pin de interrupcion del MPU6050
#define gpsOn PA11               // Pin de activacion del GPS
#define BAT0 PA0                 // Pin de tension de bateria 1
#define BAT1 PA1                 // Pin de tension de bateria 2
#define MainS PA12               // Pin Sensors enable
#define AQS PA2                  // Pin del sensor MQ-135
#define buzzer PA8               // Pin del buzzer de recuperacion
#define servoDerPin PB1          // Pin del servo derecha
#define servoIzqPin PB0          // Pin del servo izquierda
#define HW_TIMER_INTERVAL_MS 1
#define TIMER_INTERVAL_1 6L   // Intervalo1 salta cada 6 ms
#define TIMER_INTERVAL_2 500L // Intervalo2 salta cada 500 ms
#define TIMER_INTERVAL_3 50L  // Intervalo3 salta cada 50 ms
#define servoDerMaxMicros 400
#define servoDerMinMicros 2400
#define servoIzqMaxMicros 2400
#define servoIzqMinMicros 400
#define minHorizontalAcc 5000 // mm
#define USE_STM32_TIMER_NO TIM2
#define comma ','
#define memInit 0
#define memMision 1
#define memDesc 2
#define memLat 3
#define memLong 4
#define memReset 5
#define memTiempo 6
#define MPUaddress 0x68

File csvTelemetry;
STM32Timer Timer1(TIM1);
STM32_ISR_Timer ISR_Timer1_Temp;
MPU9250 mpu;
AHTxx aht10(AHTXX_ADDRESS_X38, AHT1x_SENSOR); // sensor address, sensor type
TinyGPSPlus tGPS;
BMP280_DEV bmp280;
Servo servoDer;
Servo servoIzq;

const float altitudMar = 326;
float T = 0, P = 0, giroX, giroY, giroZ, accX, accY, accZ, ahtValue, miOrientacion = 0, mx, my, mz, altitud, altitudMax = 0;
double tAnterior = 0, pAnterior = 0, latitud, longitud;
bool pressureDRDY = false, busqueda = false, finalizarMision = false, gpsDRDY = false, transmit = false, sensors = false, actualizarMpu = false, leerMpu = false, responder = false, haRespondido = false, noPudoProcesar = false, escribirDatos = false, ejecutarAccion = false, inicializacion = false, inicializado = false, enviarDevuelta = true, escritura = false, coordenadas = false, listoParaDespegar = false, descenso = false, wipeEeprom = false, iniciarMision = false;
uint8_t disparoMedicion = 0, cicloAht = 0, preparacion = 0, tiempoGps = 0;
uint16_t MQ135, batteryLevel1, batteryLevel2, deltaOrientacion, distanciaADestino, orientacionADestino, readAht = 0;
uint32_t humidity, tiempoMision;
String latitudAterrizaje, longitudAterrizaje;


void cansatStartUp();
void Timer1Handler();
void onReceive(int);
void telemetrySend();
void reportar(String);
void readSensors();
void beginMeasurementAht();
void readHumidityAht();
void leerMPU();
void loraSetup();
void bmpSetup();
void timerSetup();
void servoSetup();
void GPSSetup();
void mpuSetup();
void aht10Setup();
void sdCardSetup();
void transmitir();
void sensorsBegin();
void readMPU();
void servoControl();
void escribirArchivo();
void errorCheck(char);
bool checkSensorStatus(char);
void LoRa_Transmit(uint8_t, uint8_t, String);
void leerGPS();
double courseTo(double lat1, double long1, double lat2, double long2);
double distanceBetween(double lat1, double long1, double lat2, double long2);
void song(int);

void setup()
{
    // put your setup code here, to run once:
    // EEPROM.begin();
    pinMode(LED_BUILTIN, OUTPUT); // FUNCIONA EN LOGICA INVERSA!
    pinMode(MainS, OUTPUT);
    pinMode(gpsOn, OUTPUT);             // FUNCIONA EN LOGICA INVERSA!
    pinMode(buzzer, OUTPUT_OPEN_DRAIN); // FUNCIONA EN LOGICA INVERSA!
    pinMode(BAT0, INPUT);
    pinMode(BAT1, INPUT);
    pinMode(INTMPU, INPUT);
    pinMode(AQS, INPUT);
    digitalWrite(LED_BUILTIN, HIGH);
    digitalWrite(MainS, LOW);
    digitalWrite(buzzer, HIGH);
    digitalWrite(gpsOn, LOW);

    loraSetup(); // Setup modulo lora

    // if (EEPROM.read(memReset))
    // {
    //     reportar("Reset Exitoso");
    //     EEPROM.update(memReset, 0);
    // }

    timerSetup(); // Setup de interrupciones de timer

    attachInterrupt(digitalPinToInterrupt(INTMPU), readMPU, FALLING);
}

void loop()
{
    if (!inicializado)
    {
        // if (EEPROM.read(memInit))
        // {
        //     cansatStartUp();
        //     tiempoMision = EEPROM.read(memTiempo);
        //     descenso = EEPROM.read(memDesc);
        //     iniciarMision = EEPROM.read(memMision);
        //     latitudAterrizaje = EEPROM.read(memLat);
        //     longitudAterrizaje = EEPROM.read(memLong);
        //     inicializacion = false;
        //     inicializado = true;
        // }

        if (inicializacion)
        {
            cansatStartUp();
            haRespondido = false;
            inicializado = true;
            // EEPROM.update(memInit, true);
        }
    }
    else
    {
        if (listoParaDespegar || iniciarMision)
        {
            if (!finalizarMision)
            {

                leerGPS();

                if (pressureDRDY)
                {   
                    
                    //altitud = altitud - altitudMar;
                    if (altitud <= 0)
                        altitud = 0;

                    if (altitud >= altitudMax)
                        altitudMax = altitud;

                    /*if (altitud <= 10 && altitudMax >= 50)
                      finalizarMision = true; */

                    if(altitud < altitudMax-10){
                      descenso = true;
                     // EEPROM.update(memDesc, true);
                    }
                    

                    pressureDRDY = false;
                }

                if (cicloAht == 1)
                    beginMeasurementAht();

                if (cicloAht == 2)
                {
                    readHumidityAht();
                    cicloAht = 0;
                }
                if (transmit)
                {
                    telemetrySend();
                    transmit = false;
                }
                if (sensors)
                {
                    readSensors();
                    sensors = false;
                }
                if (descenso && gpsDRDY)
                {
                    servoControl();
                    gpsDRDY = false;
                }

                if (actualizarMpu)
                {
                    mpu.update();
                    actualizarMpu = false;
                }
                if (leerMpu)
                {

                    Wire.beginTransmission(MPUaddress);
                    Wire.write(0x3A); // Registro de status de interrupciones
                    Wire.endTransmission();
                    Wire.requestFrom(MPUaddress, (uint8_t)1); // Se pide la informacion del registro anterior

                    byte data = Wire.read();

                    if (data == 0x81)
                    {
                        leerMPU();
                        //descenso = true;
                        // EEPROM.update(memDesc, true);
                    }
                    else if (data == 0x01)
                        leerMPU();
                    else if (data == 0x80)
                    {
                        //descenso = true;
                        // EEPROM.update(memDesc, true);
                    }
                    actualizarMpu = true;
                    leerMpu = false;
                }

                if (escritura && !listoParaDespegar)
                {
                    if (csvTelemetry)
                    {
                        if (!transmit)
                        {
                            csvTelemetry.println(String(String(millis() - tiempoMision) + comma + String(altitud) + comma + String(descenso) + comma + String(T) + comma + String(P) + comma + String(giroX) + comma + String(giroY) + comma + String(miOrientacion) + comma + String(accX) + comma + String(accY) + comma + String(accZ) + comma + String(ahtValue) + comma + String(MQ135) + comma + latitud + comma + longitud + comma + String(batteryLevel1)));
                            csvTelemetry.flush();
                        }
                    }
                    else
                    {
                        reportar("Fallo al abrir archivo de MicroSD");
                    }
                    escritura = false;
                }
            }
            else
            {
                servoDer.detach();
                servoIzq.detach();
                digitalWrite(servoDerPin, LOW);
                digitalWrite(servoIzqPin, LOW);
                digitalWrite(MainS, LOW);
                if (busqueda)
                {
                    song(buzzer);
                    delay(1000);
                }
            }
        }
    }
}

void cansatStartUp()
{
    digitalWrite(MainS, HIGH);
    digitalWrite(gpsOn, LOW);

    Wire.begin();
    delay(2000);
    bmpSetup();
    delay(100);
    aht10Setup();
    delay(100);
    mpuSetup();
    delay(100);
    sdCardSetup();
    delay(100);
    GPSSetup();
    delay(100);
    servoSetup();
}

// Inicializacion del Timer
void timerSetup()
{
    // Timer1, lectura de temperatura y transmision
    Timer1.attachInterruptInterval(HW_TIMER_INTERVAL_MS * 1000, Timer1Handler);
    ISR_Timer1_Temp.setInterval(TIMER_INTERVAL_1, sensorsBegin);    // Intervalo de timer para los ciclos de lectura de sensor
    ISR_Timer1_Temp.setInterval(TIMER_INTERVAL_2, transmitir);      // Intervalo de timer para la transmision de datos a la ET
    ISR_Timer1_Temp.setInterval(TIMER_INTERVAL_3, escribirArchivo); // Intervalo de timer para escribir a la microsd
}

// Inicializacion del LoRa
void loraSetup()
{
    pinMode(RST, OUTPUT);
    digitalWrite(RST, HIGH);
    LoRa.setPins(NSS, RST, IRQ);
    // Inicializar módulo LoRa
    while (!LoRa.begin(LORA_FREQUENCY))
        ;
    LoRa.setTxPower(LORA_POWER);
    LoRa.setSpreadingFactor(LORA_SPREAD_FACTOR);
    LoRa.setSignalBandwidth(LORA_SIG_BANDWIDTH);
    LoRa.setCodingRate4(LORA_CODING_RATE);
    LoRa.setSyncWord(LORA_SYNC_WORD);

    LoRa.onReceive(onReceive);
    LoRa.receive();
}

// Inicializacion del MPU6050
void mpuSetup()
{
    errorCheck(1);

   reportar("Please leave the device still on a flat plane.");
    //mpu.verbose(true);
    //delay(5000);
    mpu.calibrateAccelGyro();

    reportar("Please Wave device in a figure eight until done.");
    //delay(5000);
    mpu.calibrateMag();

     reportar("Calibration Complete");

    Wire.beginTransmission(MPUaddress); // Se le escribe datos al mpu9250
    Wire.write(0x37);                   // Registro configuracion del pin int
    Wire.write(0xB2);
    Wire.endTransmission();

    reportar("MPU inicializado");

    actualizarMpu = true;
}

// Inicializacion del BMP280
void bmpSetup()
{
    errorCheck(3);
    bmp280.setTimeStandby(TIME_STANDBY_250MS);
    bmp280.startNormalConversion();
    bmp280.setPresOversampling(OVERSAMPLING_X4); // Set the pressure oversampling to X4
    bmp280.setTempOversampling(OVERSAMPLING_X1); // Set the temperature oversampling to X1
    bmp280.getTempPres(T, P);
    tAnterior = T;
    pAnterior = P;
    reportar("BMP inicializado");
}

// Inicializacion del AHT10
void aht10Setup()
{
    errorCheck(2);
    reportar("AHT inicializado");
}

// Inicializacion de la MicroSD
void sdCardSetup()
{
    while (!SD.begin(PB9))
    {
        reportar("No se pudo iniciar MicroSD1");
        delay(500);
    }
    csvTelemetry = SD.open("mCALCAN.csv", FILE_WRITE);
    reportar("Micro SD iniciado");
}

// Setup del modulo del GPS
void GPSSetup()
{
    Serial.begin(GPS_BAUDRATE);
    reportar("GPS inicializado");
}

// Setup de los servos
void servoSetup()
{
    servoDer.attach(servoDerPin);
    servoIzq.attach(servoIzqPin);
}

// Subortina ISR para interrupciones
void Timer1Handler()
{
    ISR_Timer1_Temp.run();
}

// Funcion estandard para enviar mensajes por LoRa con el Protocolo gVIE
void LoRa_Transmit(uint8_t type, String reqs, String data)
{
    digitalWrite(LED_BUILTIN, LOW);
    LoRa.beginPacket();
    LoRa.print(String("gvie," + String(type) + comma + String(reqs) + comma + data));
    LoRa.endPacket(true);
    LoRa.receive();
    digitalWrite(LED_BUILTIN, HIGH);
}

// Funcion de transmision de datos a la Estacion Terrena
void transmitir()
{
    transmit = true; // Se transmiten datos a la estacion terrena
    if (!haRespondido)
    {
        enviarDevuelta = !enviarDevuelta; // Si han pasado 1000 ms, y no se respondio al comando, se vuelve a enviar
    }
    if (inicializado && listoParaDespegar)
        preparacion++;
    if (preparacion >= 31)
    {
        listoParaDespegar = false;
        preparacion = 0;
    }
}

// Funcion que envia la telemetria por el modulo LoRa a la estacion terrena
void telemetrySend()
{
    LoRa_Transmit(1, "14", String(String(T) + comma + String(P) + comma + String(giroX) + comma + String(giroY) + comma + String(miOrientacion) + comma + String(accX) + comma + String(accY) + comma + String(accZ) + comma + String(batteryLevel1) + comma + String(millis() - tiempoMision) + comma + String(descenso) + comma + String(MQ135) + comma + String(ahtValue) + comma + String(latitud, 6) + comma + String(longitud, 6) + comma + String(batteryLevel2) + comma + String(altitud)));
}

// Funcion encargada de realizar las operaciones necesarias al recibir informacion por el modulo LoRa
void onReceive(int packetSize)
{
    String LoRaData = LoRa.readString();
    Serial.println(LoRaData);

    // Busca y almacena la posicion (estilo arreglo) del caracter ingresado + X posiciones
    uint8_t confirmacion0 = LoRaData.indexOf(',');            // Header
    uint8_t tipo1 = LoRaData.indexOf(',', confirmacion0 + 1); // Tipo de mensaje
    uint8_t codigo2 = LoRaData.indexOf(',', tipo1 + 1);       // Codigo de solicitud/respuesta

    // Situa el cursor en X y extrae caracteres hasta Y
    String strconf1 = LoRaData.substring(0, confirmacion0);
    String tipomsg = (LoRaData.substring(confirmacion0 + 1, tipo1));
    String codigomsg = (LoRaData.substring(tipo1 + 1, codigo2));

    if (strconf1 == "gvie")
    { // Verifica si la informacion reciciba viene de nuestro lora a partir de la cadena de comienzo
        switch (tipomsg.toInt())
        { // Puede ser 0, 1, 2, o 3
        case 0:
            responder = true; // Se espera que el mensaje sea de tipo confirmable (Se confirma con "OK")
            break;

        case 1:
            responder = false; // Se espera que el mensaje sea de tipo no confirmable
            haRespondido = false;
            break;

        case 2:
            haRespondido = true; // Significa que el paquete enviado es para confirmar un comando
            break;

        default:
            break;
        }

        if (!haRespondido)
        {
            switch (codigomsg.toInt())
            {

            case 3:
                inicializacion = true;
                listoParaDespegar = true;
                break;

            case 12:
                coordenadas = true;
                break;

            case 20:
                digitalWrite(gpsOn, HIGH);
                tiempoMision = millis();
                iniciarMision = true;
                // EEPROM.update(memMision, true);
                break;

            case 21:
                latitudAterrizaje = latitud;
                longitudAterrizaje = longitud;
                break;

            case 26:
                finalizarMision = true;
                busqueda = true;
                break;

            case 35:
                wipeEeprom = true;
                break;

            case 37:
                // EEPROM.put(memTiempo, (millis() - tiempoMision));
                // EEPROM.update(memReset, 1);
                digitalWrite(MainS, LOW);
                NVIC_SystemReset(); // El mensaje recibido es para resetear el sistema
                break;

            case 77:
                // Indefinido
                break;

            default:
                LoRa_Transmit(3, "77", "");
                break;
            }
        }
        if (responder)
        {
            LoRa_Transmit(2, codigomsg, "");
            responder = false;
        }
        if (coordenadas)
        {
            uint8_t indicador1 = LoRaData.indexOf(',', codigo2 + 1); // Datos
            uint8_t indicador2 = LoRaData.indexOf(',', indicador1 + 1);
            latitudAterrizaje = LoRaData.substring(codigo2 + 1, indicador1);
            longitudAterrizaje = LoRaData.substring(indicador1 + 1, indicador2);
            // EEPROM.put(memLat, latitudAterrizaje);
            // EEPROM.put(memLong, longitudAterrizaje);
            coordenadas = false;
        }
        if (!inicializacion)
        {
            if (codigomsg.toInt() == 20)
                LoRa_Transmit(3, "77", "");
        }
        if (!listoParaDespegar)
        {
            if (codigomsg.toInt() == 03)
                LoRa_Transmit(3, "77", "");
        }
        if (!iniciarMision)
        {
            if (codigomsg.toInt() == 00)
                LoRa_Transmit(3, "77", "");
        }
        if (wipeEeprom)
        {
            // for (int i = 0; i < (memTiempo + 1); i++)
            //     EEPROM.put(i, false);
            wipeEeprom = false;
        }
    }
}

// Funcion basica de envio de errores a la Estacion Terrena
void reportar(String data)
{
    LoRa_Transmit(4, "77", String(data));
}

// Se completa un ciclo de la lectura de sensores
void sensorsBegin()
{
    sensors = true;
}

// Funcion que lee todos los sensores a su maxima velocidad. Controlada por banderas de interrupcion
void readSensors()
{
    readAht++;
    if (readAht == 1)
        cicloAht++;

    if (readAht == 16)
        cicloAht++;

    if (readAht >= 400)
        readAht = 0;

    switch (disparoMedicion)
    {
    case 0:
        batteryLevel1 = (analogRead(BAT0) * 1.2);
        MQ135 = analogRead(AQS);
        batteryLevel2 = (analogRead(BAT1) * 1.2);
        disparoMedicion++;
        break;

    case 1:
        bmp280.getCurrentMeasurements(T, P, altitud);
        pressureDRDY = true;
        disparoMedicion = 0;
        break;

    default:
        disparoMedicion = 0;
        break;
    }
}

// Funcion callback del pin INT para iniciar la lectura del MPU6050
void readMPU()
{
    leerMpu = true; // Comienza la actualizacion de datos del MPU6050
}

// Lectura de los datos del sensor MPU6050
void leerMPU()
{
    accX = mpu.getAccX();
    accY = mpu.getAccY();
    accZ = mpu.getAccZ();
    if (accX >= 3 || accY >= 3 || accZ >= 3)
        digitalWrite(gpsOn, HIGH);
    else
        digitalWrite(gpsOn, LOW);
    giroX = mpu.getGyroX();
    giroY = mpu.getGyroY();
    giroZ = mpu.getGyroZ();
    mx = mpu.getMagX();
    my = mpu.getMagY();
    mz = mpu.getMagZ();

    miOrientacion = atan2(my, mx) * RAD_TO_DEG;
    miOrientacion < 0 ? 360 + miOrientacion : miOrientacion;

    deltaOrientacion = orientacionADestino - miOrientacion;
    deltaOrientacion = (deltaOrientacion < (-180)) ? deltaOrientacion + 360 : deltaOrientacion;
    deltaOrientacion = (deltaOrientacion > 180) ? deltaOrientacion - 360 : deltaOrientacion;
}

// Lectura de los datos del sensor de GPS
void leerGPS()
{
    while (Serial.available())
    {
        if (tGPS.encode(Serial.read()))
        {

            longitud = (tGPS.location.lng());

            latitud = (tGPS.location.lat());

            if (tGPS.location.isValid() && (tGPS.hdop.hdop() < 2))
            {
                distanciaADestino = distanceBetween(latitud, longitud, latitudAterrizaje.toDouble(), longitudAterrizaje.toDouble());
                orientacionADestino = courseTo(latitud, longitud, latitudAterrizaje.toDouble(), longitudAterrizaje.toDouble());
                gpsDRDY = true;
            }
            else
            {
                servoIzq.write(servoIzqMinMicros);
                servoDer.write(servoDerMinMicros);
            }
        }
    }
}

// Ceba el AHT para que comienze una medicion y despues leer los datos recuperados
void beginMeasurementAht()
{
    Wire.beginTransmission(0x38);

    Wire.write(AHTXX_START_MEASUREMENT_REG);      // send measurement command, strat measurement
    Wire.write(AHTXX_START_MEASUREMENT_CTRL);     // send measurement control
    Wire.write(AHTXX_START_MEASUREMENT_CTRL_NOP); // send measurement NOP control

    Wire.endTransmission(true);
}
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

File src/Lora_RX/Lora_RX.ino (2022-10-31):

/* 
Codigo hecho por alumnos del ITS Villada 7° año B, Electronica. Año 2022
Placa: Adafruit LoRa 32u4

*/

#include <SPI.h>
#include <LoRa.h>
#include <string.h>
#include <EEPROM.h>

// Defino los pines a ser usados por el modulo transceptor LoRa
#define CS 8                 // Pin de CS del módulo LoRa
#define RST 4                // Pin de Reset del módulo LoRa
#define IRQ 7                // Pin del IRQ del módulo LoRa
#define LED 13               // Pin del LED onboard
#define SERIAL_BAUDRATE 9600 // Velocidad del Puerto Serie

#define LORA_FREQUENCY 915000000
#define LORA_SYNC_WORD 0xDE
#define LORA_POWER 19            // TX power in dB, defaults to 17.
#define LORA_SPREAD_FACTOR 7     // Spreading factor, defaults to 7. Supported values are between 6 and 12 (En Argentina se puede utilizar entre 7 a 10)
#define LORA_SIG_BANDWIDTH 125E3 // Signal bandwidth in Hz, defaults to 125E3. Supported values are 7.8E3, 10.4E3, 15.6E3, 20.8E3, 31.25E3, 41.7E3, 62. 5E3, 125E3, 250E3, and 500E3
#define LORA_CODING_RATE 5
#define DATA_TIME 500

#define comma ','

#define intervalo 1500

bool responder = false, error = false, cansatReset = false, telemetria = false, serial = false;
uint8_t comandoFracasado;
String LoRaData, presion, data = "", recepcionSerial, latencia;

void (*resetFunc)(void) = 0;
void LoRa_Transmit(uint8_t, uint8_t, String);

void setup()
{
    // Set Led onboard con Output
    pinMode(LED, OUTPUT);
    // Incializo el Serial Monitor
    Serial.begin(SERIAL_BAUDRATE);
    EEPROM.begin();
    // Turn on the transmission, reception, and Receive interrupt
    while (!Serial)
    {
        // Mientras el COM no esté disponible el LED onbooard encendido
        digitalWrite(LED, HIGH);
    }
    // Apaga el LED si se conecta al COM
    digitalWrite(LED, LOW);
    Serial.println("LoRa Receiver");
    // Inicializar módulo LoRa
    LoRa.setPins(CS, RST, IRQ);
    while (!LoRa.begin(LORA_FREQUENCY))
    {
        Serial.println(".");
        delay(DATA_TIME);
    }
    // Change sync word (0xF3) to match the receiver
    // The sync word assures you don't get LoRa messages from other LoRa transceivers
    // ranges from 0-0xFF
    LoRa.setSyncWord(LORA_SYNC_WORD);
    LoRa.setTxPower(LORA_POWER);
    LoRa.setSpreadingFactor(LORA_SPREAD_FACTOR);
    LoRa.setSignalBandwidth(LORA_SIG_BANDWIDTH);
    LoRa.setCodingRate4(LORA_CODING_RATE);

    Serial.println("LoRa Initializing OK!");
    LoRa.onReceive(onReceive);
    LoRa.receive();
}

void loop()
{
    if (Serial.available())
    {
        recepcionSerial = Serial.readString();
        recepcionSerial.trim();
        serial = true;
    }
    if (serial)
    {
        LoRa.beginPacket();
        LoRa.print(recepcionSerial);
        LoRa.endPacket(true);
        LoRa.receive();
        serial = false;
    }
}

void onReceive(int packetSize)
{
    String LoRaData = LoRa.readString();

    int confirmacion0 = LoRaData.indexOf(',');            // Header
    int tipo1 = LoRaData.indexOf(',', confirmacion0 + 1); // Tipo de mensaje
    int codigo2 = LoRaData.indexOf(',', tipo1 + 1);       // Codigo de solicitud/respuesta

    String strconf1 = LoRaData.substring(0, confirmacion0);
    String tipomsg = LoRaData.substring(confirmacion0 + 1, tipo1);
    String codigomsg = LoRaData.substring(tipo1 + 1, codigo2);

    // Desglosaje del protocolo GVIE
    if (strconf1 == "gvie")
    { // Verifica si la informacion reciciba viene de nuestro lora a partir de la cadena de comienzo

        switch (tipomsg.toInt()) // Puede ser 0, 1, 2, o 3
        {
        case 0:
            responder = true; // Se espera que el mensaje sea de tipo confirmable (Se confirma con "OK")
            break;

        case 1:
            responder = false; // Se espera que el mensaje sea de tipo no confirmable
            break;

        case 2:
            Serial.println(LoRaData);
            break;

        case 3:
            Serial.println(LoRaData);
            break;

        case 4:
            error = true;
            break;

        default:
            break;
        }

        switch (codigomsg.toInt())
        {

        case 37:
            resetFunc(); // El mensaje recibido es para resetear el sistema
            break;

        case 14:
            telemetria = true;
            break;

        case 77:
            // Indefinido
            break;

        default:
            break;
        }

        // Recepcion de telemetria raw
        if (telemetria)
        {
            int indicador1 = LoRaData.indexOf(',', codigo2 + 1); // Datos
            int indicador2 = LoRaData.indexOf(',', indicador1 + 1);
            int indicador3 = LoRaData.indexOf(',', indicador2 + 1);
            int indicador4 = LoRaData.indexOf(',', indicador3 + 1);
            int indicador5 = LoRaData.indexOf(',', indicador4 + 1);
            int indicador6 = LoRaData.indexOf(',', indicador5 + 1);
            int indicador7 = LoRaData.indexOf(',', indicador6 + 1);
            int indicador8 = LoRaData.indexOf(',', indicador7 + 1);
            int indicador9 = LoRaData.indexOf(',', indicador8 + 1);
            int indicador10 = LoRaData.indexOf(',', indicador9 + 1);
            int indicador11 = LoRaData.indexOf(',', indicador10 + 1);
            int indicador12 = LoRaData.indexOf(',', indicador11 + 1);
            int indicador13 = LoRaData.indexOf(',', indicador12 + 1);
            int indicador14 = LoRaData.indexOf(',', indicador13 + 1);
            int indicador15 = LoRaData.indexOf(',', indicador14 + 1);
            int indicador16 = LoRaData.indexOf(',', indicador15 + 1);
            int indicador17 = LoRaData.indexOf(',', indicador16 + 1);

            String temperatura = LoRaData.substring(codigo2 + 1, indicador1);

            String presion = LoRaData.substring(indicador1 + 1, indicador2);

            String giro1 = LoRaData.substring(indicador2 + 1, indicador3);
            String giro2 = LoRaData.substring(indicador3 + 1, indicador4);
            String giro3 = LoRaData.substring(indicador4 + 1, indicador5);

            String vel1 = LoRaData.substring(indicador5 + 1, indicador6);
            String vel2 = LoRaData.substring(indicador6 + 1, indicador7);
            String vel3 = LoRaData.substring(indicador7 + 1, indicador8);

            String bat = LoRaData.substring(indicador8 + 1, indicador9);

            String tiempo = LoRaData.substring(indicador9 + 1, indicador10);

            String caidaLibre = LoRaData.substring(indicador10 + 1, indicador11);

            String calidadDeAire = LoRaData.substring(indicador11 + 1, indicador12);

            String humedad = LoRaData.substring(indicador12 + 1, indicador13);

            String latitud = LoRaData.substring(indicador13 + 1, indicador14);

            String longitud = LoRaData.substring(indicador14 + 1, indicador15);

            String bat2 = LoRaData.substring(indicador15 + 1, indicador16);

            String altitud = LoRaData.substring(indicador16 + 1, indicador17);
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

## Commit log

2022-08-12 Update Lora_TX.ino
    Es el codigo para empezar la mision secundaria
2022-08-24 Update Lora_RX.ino
    Ya le cambie los valores a las variables booleanas, y le agrego el sensor de calidad de aire
2022-08-28 Update Lora_TX.ino
    Reducido un poco el tamaño del programa (95% a 86%)
    Repetitividad reducida con el uso de funciones
    Codigo acomodado
    Prototipos agregados
    Ahora se usa un puerto SPI fisico para la MicroSD (antes era por software)
    Ahora funciona la telemetria local en MicroSD
    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
2022-08-28 Delete arduino-LoRa-STM32-master.zip
    Libreria en desuso reemplazada por la estandard de arduino
2022-08-28 Update Lora_TX.ino
    Optimizado aun mas el uso de la memoria estatica (86 a 84%)
    Ahora no abrimos y cerramos el mismo archivo por cada linea que escribimos. Una vez abierto, usamos File.flush() para pasar todo a la MicroSD y liberar memoria dinamica
    Los tiempos de escritura tienen una falla periodica que duplica su tiempo de escritura
    Cambiamos la libreria SDFat por la libreria estandard de arduino SD (mas liviana, menos compleja)
2022-08-29 Codigo provisional Flyback
    Código provisional del flyback, sin control de servos
2022-09-02 optimized flyback code
    Para optimizar el uso de recursos se cambio el protocolo del GPS de NMEA a UBX y se usa una librería mas ligera.
2022-09-06 Updated fly-back code
    Se añado el control de servos al código de prueba de flyback y se realizaron cambios de optimización
2022-09-06 Carpetas nuevas
    Agregada carpeta con las librerias utilizadas y carpeta con recursos extras para la configuracion del cansat (GPS y compas)
2022-09-14 libraries updates
    cambios en las librerias: Se elimino la libreria ServoTiemr2 y se actualizo CustomQMC5883L
2022-09-18 Add files via upload
    Cambio para usar SPI2
2022-09-22 borrado de archivos redundantes
2022-09-22 borrado de librerías no utilizadas
2022-09-22 borrado de librerías redundantes
2022-09-22 uploaded 3d print models
    [Antena.SLDPRT, Carcasa ET abajo.STL, Carcasa ET arriba.SLDPRT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]
2023-11-23 Agrega fuente de los esquemáticos y diseños de pcb
    [53253-0270.step, 53253-0270.stp, AHT10 Breakout.step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]
